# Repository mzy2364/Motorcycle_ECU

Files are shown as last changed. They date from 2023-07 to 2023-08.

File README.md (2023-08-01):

# Motorcycle_ECU

单缸摩托车发送机控制单元

视频地址 : <a href="https://www.bilibili.com/video/BV1r14y167MM/">https://www.bilibili.com/video/BV1r14y167MM/</a> 

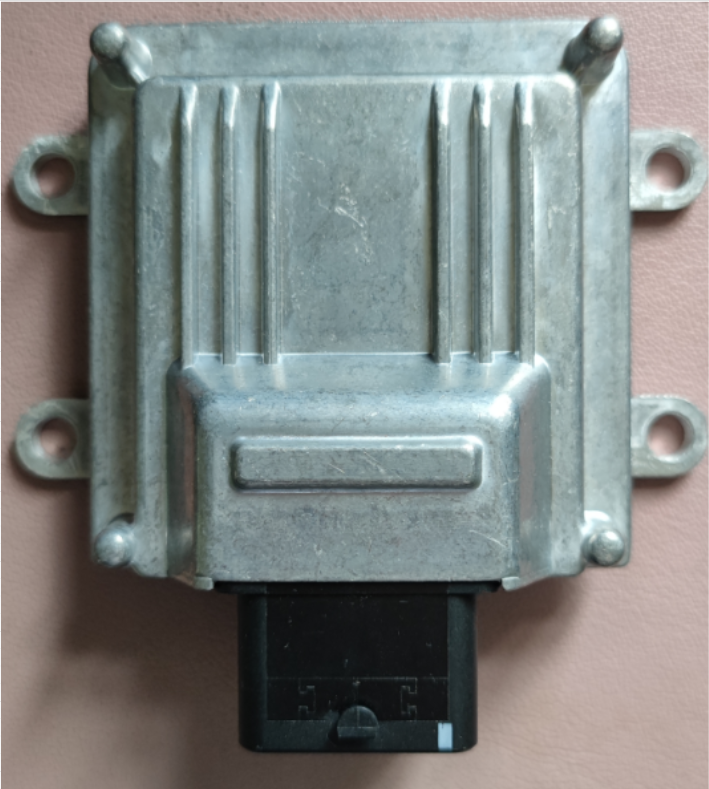
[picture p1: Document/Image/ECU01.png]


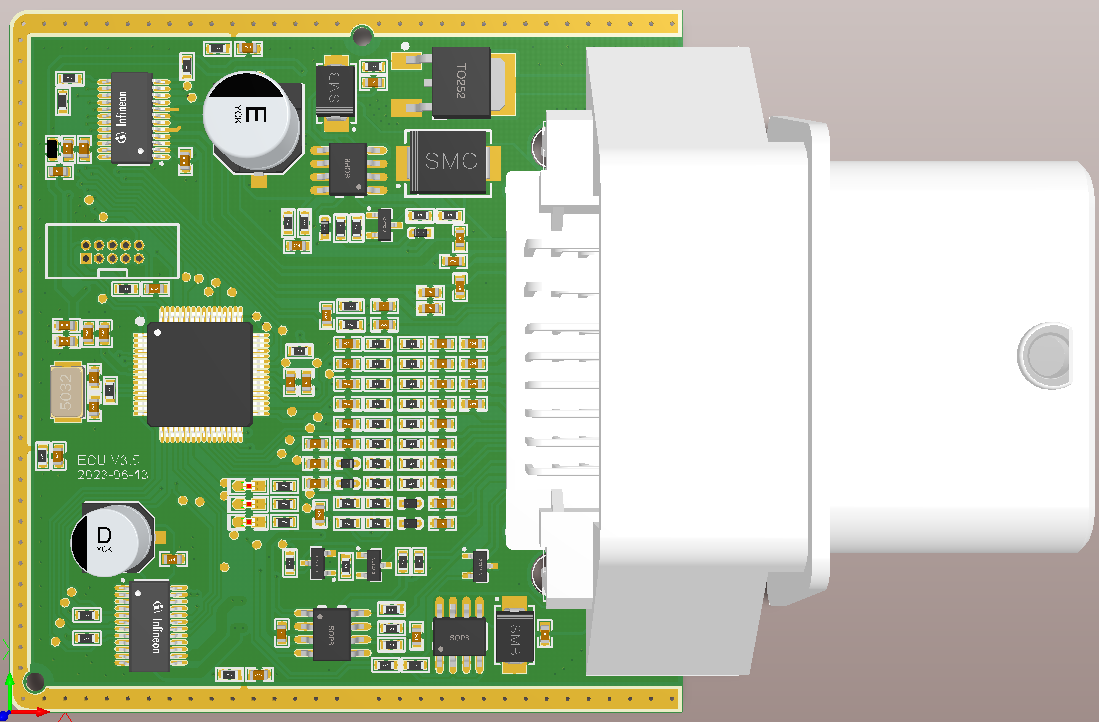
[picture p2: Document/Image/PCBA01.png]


### 支持功能

曲轴信号识别

点火线圈控制

喷油器控制

怠速电机控制

CAN 通讯

转速信号输出 / PWM输出

IgnON、Engine Stop 等开关识别

节气门位置传感器、进气歧管压力传感器、空气温度传感器、缸体温度传感器、氧传感器等

氧传感器加热

MIL 灯控制、继电器输出、燃油泵控制、怠速阀控制

### 硬件结构

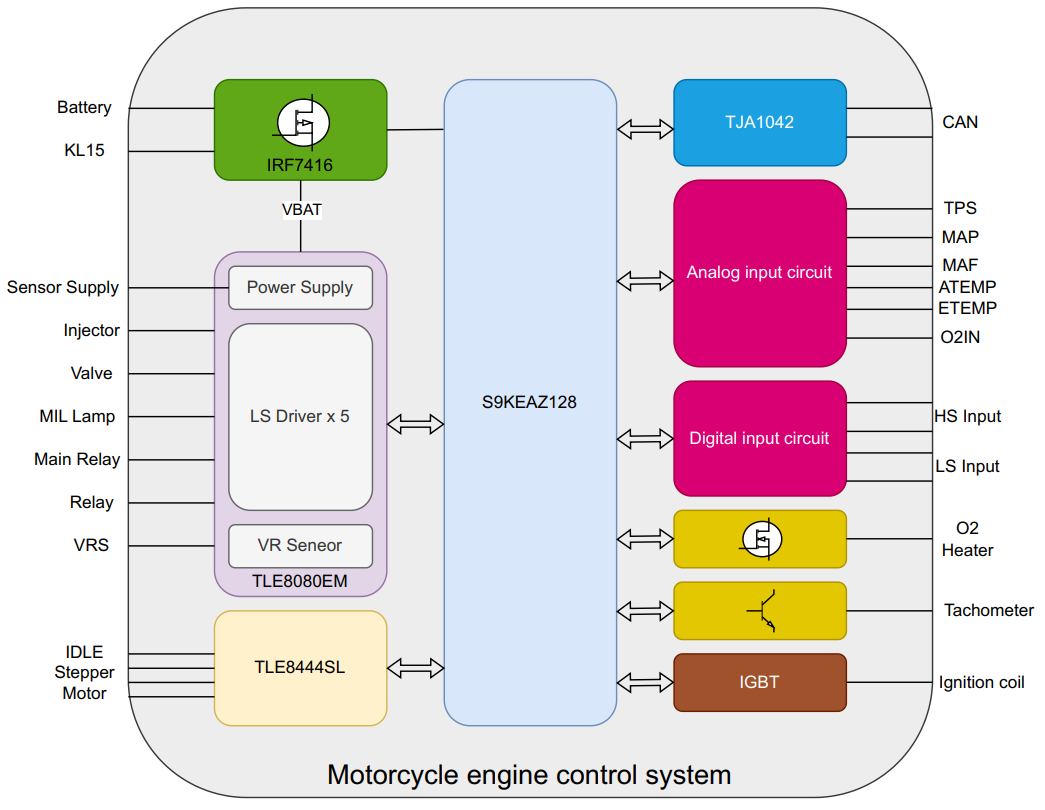
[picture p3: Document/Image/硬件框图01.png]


### 软件功能

仅提供支持发动机运转的基本功能，包括：

曲轴位置识别

喷油角度和脉宽计算

点火角度和蓄能时间计算

根据曲轴位置控制点火和喷油

根据进气歧管压力传感器识别冲程

CAN通讯，关键信息发送，基于 CAN 的简单标定

转速脉冲信号输出

燃油泵驱动

### 参考资料

https://www.nxp.com.cn/applications/automotive/electrification-and-powertrain/motorcycle-engine-control-unit-ecu-and-small-engine-control:MOTORCYCLE-ECU-SMALL-ENGINE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

https://www.st.com/zh/applications/powertrain-for-ice/single-cylinder-motorcycle-engine.html

https://www.infineon.com/cms/cn/applications/automotive/powertrain-systems/small-1-cylinder-combustion-engine-solution/

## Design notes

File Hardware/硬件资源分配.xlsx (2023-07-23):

LQFP64 | Pin Name | 默认值 | ALT0 | ALT1 | ALT2 | ALT3 | ALT4 | ALT5 | 所选资源 | 引脚网络名 | 功能区域
1 | PTD1 | 禁用 | PTD1 | KBI0_P25 | FTM2_CH3 | SPI1_MOSI |  |  | FTM2_CH3 | VRSOUT | 曲轴信号采集
2 | PTD0 | 禁用 | PTD0 | KBI0_P24 | FTM2_CH2 | SPI1_SCK |  |  | FTM2_CH2 |  | 曲轴缺齿中断用
3 | PTH7 | 禁用 | PTH7 | KBI1_P31 | PWT_IN1 |  |  |  | GPIO
4 | PTH6 | 禁用 | PTH6 | KBI1_P30 |  |  |  |  | GPIO
5 | PTE7 | 禁用 | PTE7 | KBI1_P7 | TCLK2 | FTM1_CH1 | CAN0_TX |  | GPIO/FTM1_CH1 | O_F_CH01/M | PWM以及转速信号输出
6 | PTH2 | 禁用 | PTH2 | KBI1_P26 | BUSOUT | FTM1_CH0 | CAN0_RX |  | FTM1_CH0 | O2HIN | 氧传感器加热
7 | VDD | VDD | VDD |  |  |  |  |  | VDD |  | 系统及电源
8 | VDDA | VDDA | VREFH | VDDA |  |  |  |  | VDD |  | 系统及电源
9 | VREFL | VREFL | VREFL |  |  |  |  |  | GND |  | 系统及电源
10 | VSS/ VSSA | VSS/ VSSA | VSSA | VSS |  |  |  |  | GND |  | 系统及电源
11 | PTB7 | EXTAL | PTB7 | KBI0_P15 | I2C0_SCL | EXTAL |  |  | OSC |  | 系统及电源
12 | PTB6 | XTAL | PTB6 | KBI0_P14 | I2C0_SDA | XTAL |  |  | OSC |  | 系统及电源
13 | PTI4 | 禁用 | PTI4 | IRQ
14 | PTH1 | 禁用 | PTH1 | KBI1_P25 | FTM2_CH1
15 | PTH0 | 禁用 | PTH0 | KBI1_P24 | FTM2_CH0
16 | PTE6 | 禁用 | PTE6 | KBI1_P6 |  |  |  |  | GPIO | MOTOR_EF2 | 电机驱动故障反馈
17 | PTE5 | 禁用 | PTE5 | KBI1_P5 |  |  |  |  | GPIO | MOTOR_IN2 | 电机驱动
18 | PTB5 | 禁用 | PTB5 | KBI0_P13 | FTM2_CH5 | SPI0_PCS | ACMP1_OUT |  | GPIO | MOTOR_EF1 | 电机驱动故障反馈
19 | PTB4 | NMI_b | PTB4 | KBI0_P12 | FTM2_CH4 | SPI0_MISO | ACMP1_IN2 | NMI_b | GPIO | MOTOR_IN4 | 电机驱动
20 | PTC3 | ADC0_SE11 | PTC3 | KBI0_P19 | FTM2_CH3 | ADC0_SE11 |  |  | GPIO | MOTOR_INH | 电机驱动使能
21 | PTC2 | ADC0_SE10 | PTC2 | KBI0_P18 | FTM2_CH2 | ADC0_SE10 |  |  | GPIO | LED_B | LED_B
22 | PTD7 | 禁用 | PTD7 | KBI0_P31 | UART2_TX |  |  |  | GPIO | LED_G | LEB_G
23 | PTD6 | 禁用 | PTD6 | KBI0_P30 | UART2_RX |  |  |  | GPIO | LED_R | LEB_R
24 | PTD5 | 禁用 | PTD5 | KBI0_P29 | PWT_IN0 |  |  |  | GPIO/PWT_IN0 | I_S_CH04/M | 高低边输入CH4
25 | PTC1 | ADC0_SE9 | PTC1 | KBI0_P17 | FTM2_CH1 | ADC0_SE9
26 | PTC0 | ADC0_SE8 | PTC0 | KBI0_P16 | FTM2_CH0 | ADC0_SE8 |  |  | GPIO | I_S_CH03/M | 高低边输入CH3
27 | PTF7 | ADC0_SE15 | PTF7 | KBI1_P15 | ADC0_SE15 |  |  |  | GPIO | I_S_CH01/M | 高低边输入CH1
28 | PTF6 | ADC0_SE14 | PTF6 | KBI1_P14 | ADC0_SE14 |  |  |  | GPIO | I_S_CH02/M | 高低边输入CH2
29 | PTF5 | ADC0_SE13 | PTF5 | KBI1_P13 | ADC0_SE13 |  |  |  | ADC0_SE13 | ETEMP_M | 模拟量输入ETEMP
30 | PTF4 | ADC0_SE12 | PTF4 | KBI1_P12 | ADC0_SE12 |  |  |  | ADC0_SE12 | TPS_M | 模拟量输入TPS
31 | PTB3 | ADC0_SE7 | PTB3 | KBI0_P11 | SPI0_MOSI | FTM0_CH1 | ADC0_SE7 |  | FTM0_CH1 | MOTOR_IN3 | 电机驱动
32 | PTB2 | ADC0_SE6 | PTB2 | KBI0_P10 | SPI0_SCK | FTM0_CH0 | ADC0_SE6 |  | FTM0_CH0 | MOTOR_IN1 | 电机驱动
33 | PTB1 | ADC0_SE5 | PTB1 | KBI0_P9 | UART0_TX | ADC0_SE5 |  |  | ADC0_SE5 | ATEMP_M | 模拟量输入ATEMP
34 | PTB0 | ADC0_SE4 | PTB0 | KBI0_P8 | UART0_RX | PWT_IN1 | ADC0_SE4 |  | ADC0_SE4 | MAF_M | 模拟量输入MAF
35 | PTF3 | 禁用 | PTF3 | KBI1_P11 | UART1_TX
36 | PTF2 | 禁用 | PTF2 | KBI1_P10 | UART1_RX
37 | PTA7 | ADC0_SE3 | PTA7 | KBI0_P7 | FTM2_FLT2 | ACMP1_IN1 | ADC0_SE3 |  | ADC0_SE3 | O2IN_M | 模拟量输入O2IN
38 | PTA6 | ADC0_SE2 | PTA6 | KBI0_P6 | FTM2_FLT1 | ACMP1_IN0 | ADC0_SE2 |  | ADC0_SE2 | MAP_M | 模拟量输入MAP
39 | PTE4 | 禁用 | PTE4 | KBI1_P4
40 | VSS | VSS | VSS |  |  |  |  |  | GND |  | 系统及电源
41 | VDD | VDD | VDD |  |  |  |  |  | VDD |  | 系统及电源
42 | PTF1 | 禁用 | PTF1 | KBI1_P9 | FTM2_CH1 |  |  |  | FTM2_CH1 | COIL_DRV | 点火线圈驱动
43 | PTF0 | 禁用 | PTF0 | KBI1_P8 | FTM2_CH0 |  |  |  | FTM2_CH0 | INJ_CTRL | 喷油嘴驱动
44 | PTD4 | 禁用 | PTD4 | KBI0_P28
45 | PTD3 | 禁用 | PTD3 | KBI0_P27 | SPI1_PCS
46 | PTD2 | 禁用 | PTD2 | KBI0_P26 | SPI1_MISO |  |  |  |  | VCC_CTRL | 电源使能
47 | PTA3 | 禁用 | PTA3 | KBI0_P3 | UART0_TX | I2C0_SCL
48 | PTA2 | 禁用 | PTA2 | KBI0_P2 | UART0_RX | I2C0_SDA |  |  | GPIO
49 | PTA1 | ADC0_SE1 | PTA1 | KBI0_P1 | FTM0_CH1 | I2C0_ 4WSDAOUT | ACMP0_IN1 | ADC0_SE1 | ADC0_SE1 | VBAT_ADC | 电源电压采集
50 | PTA0 | ADC0_SE0 | PTA0 | KBI0_P0 | FTM0_CH0 | I2C0_ 4WSCLOUT | ACMP0_IN0 | ADC0_SE0 | GPIO | VALVE_CTRL | 怠速阀控制
51 | PTC7 | 禁用 | PTC7 | KBI0_P23 | UART1_TX | CAN0_TX |  |  | CAN0_TX | CAN_TX | CAN
52 | PTC6 | 禁用 | PTC6 | KBI0_P22 | UART1_RX | CAN0_RX |  |  | CAN0_RX | CAN_RX | CAN
53 | PTE3 | 禁用 | PTE3 | KBI1_P3 | SPI0_PCS |  |  |  | SPI0_PCS | SPI_CS | TLE8080-SPI驱动
54 | PTE2 | 禁用 | PTE2 | KBI1_P2 | SPI0_MISO | PWT_IN0 |  |  | SPI0_MISO | SPI_MISO | TLE8080-SPI驱动
55 | PTG3 | 禁用 | PTG3 | KBI1_P19
56 | PTG2 | 禁用 | PTG2 | KBI1_P18
57 | PTG1 | 禁用 | PTG1 | KBI1_P17
58 | PTG0 | 禁用 | PTG0 | KBI1_P16
59 | PTE1 | 禁用 | PTE1 | KBI1_P1 | SPI0_MOSI | I2C1_SCL |  |  | SPI0_MOSI | SPI_MOSI | TLE8080-SPI驱动
60 | PTE0 | 禁用 | PTE0 | KBI1_P0 | SPI0_SCK | TCLK1 | I2C1_SDA |  | SPI0_SCK | SPI_SCK | TLE8080-SPI驱动
61 | PTC5 | 禁用 | PTC5 | KBI0_P21 | FTM1_CH1 | RTC_CLKOUT
62 | PTC4 | SWD_CLK | PTC4 | KBI0_P20 | RTC_CLKOUT | FTM1_CH0 | ACMP0_IN2 | SWD_CLK | SWCLK |  | 系统及电源
63 | PTA5 | RESET_b | PTA5 | KBI0_P5 | IRQ | TCLK0 | RESET_b |  | RESET |  | 系统及电源
64 | PTA4 | SWD_DIO | PTA4 | KBI0_P4 | ACMP0_OUT | SWD_DIO |  |  | SWDIO |  | 系统及电源

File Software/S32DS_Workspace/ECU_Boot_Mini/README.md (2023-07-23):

# ECU_Boot_Mini

ECU 最小 Boot，仅提供跳转功能，不支持 APP 更新

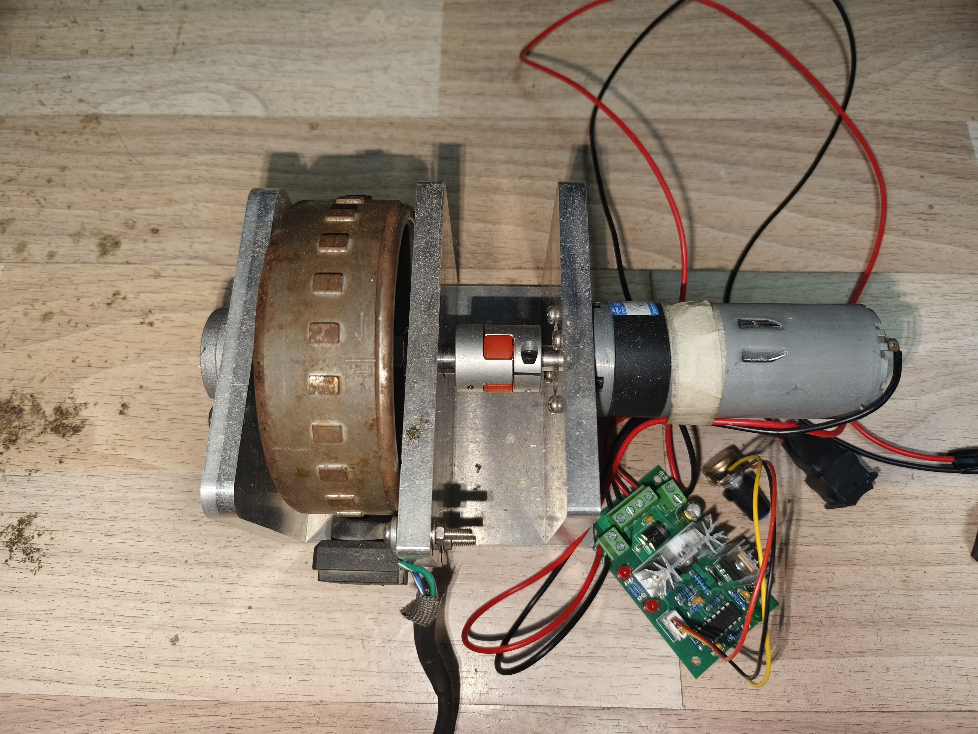
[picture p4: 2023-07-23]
Hardware/曲轴模拟器.jpg

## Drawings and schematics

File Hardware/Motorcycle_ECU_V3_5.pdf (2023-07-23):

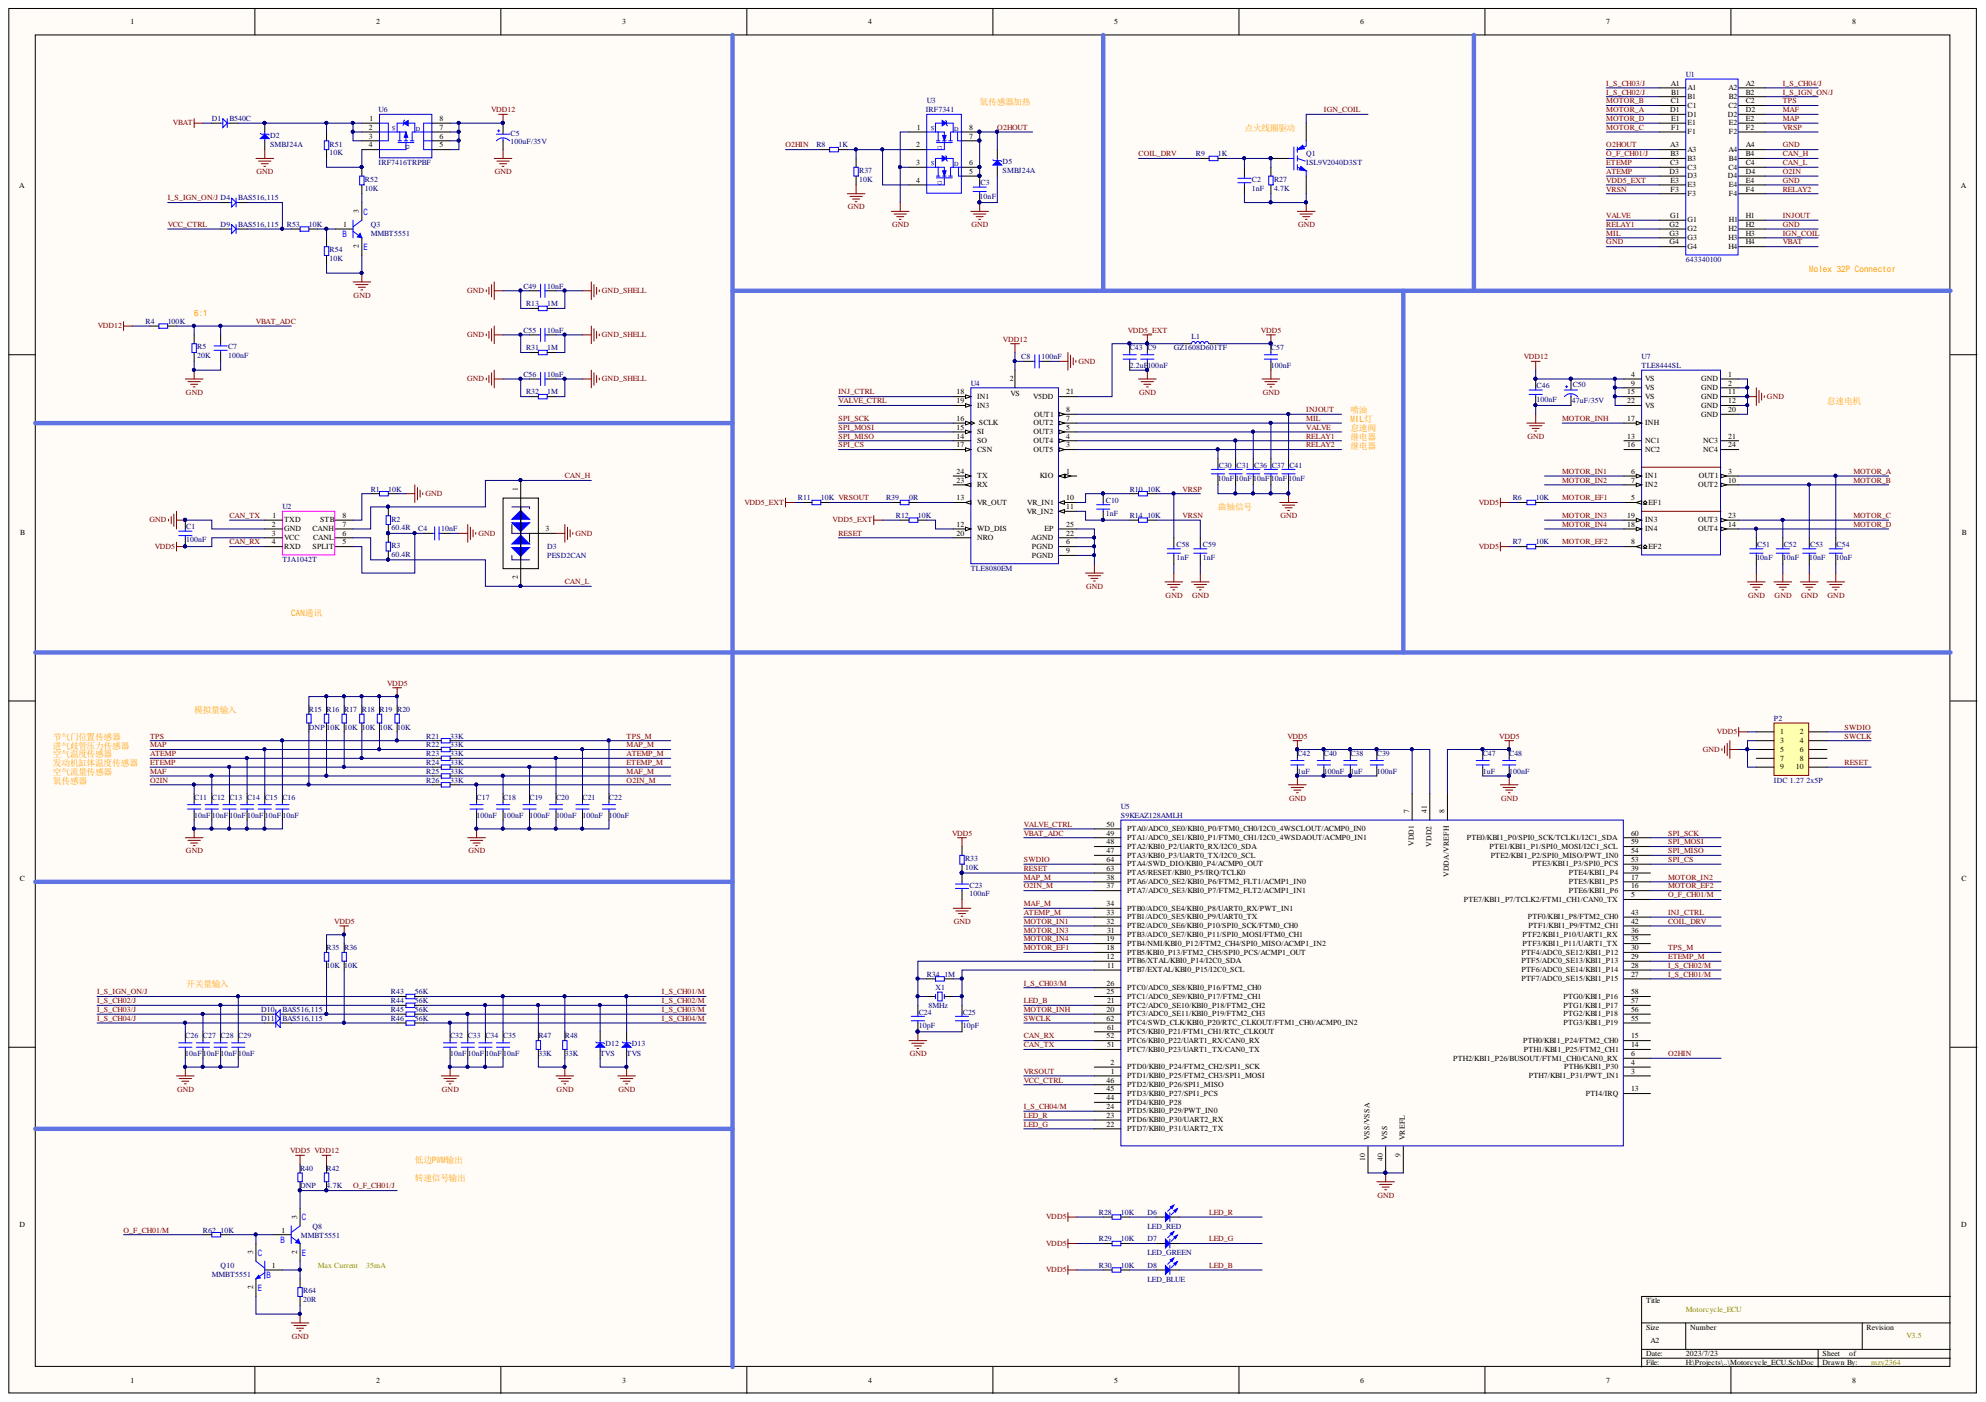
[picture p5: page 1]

IL灯 怠速阀 继电器 继电器

节气门位置传感器
进气歧管压力传感器 空气温度传感器 发动机缸体温度传感器 空气流量传感器

PTB7/EXTAL/KBI0_P15/I2C0_SCL 11

I_S_CH03/M LED_B | PTC0/ADC0_SE8/KBI0_P16/FTM2_CH0 26 PTC1/ADC0_SE9/KBI0_P17/FTM2_CH1 25

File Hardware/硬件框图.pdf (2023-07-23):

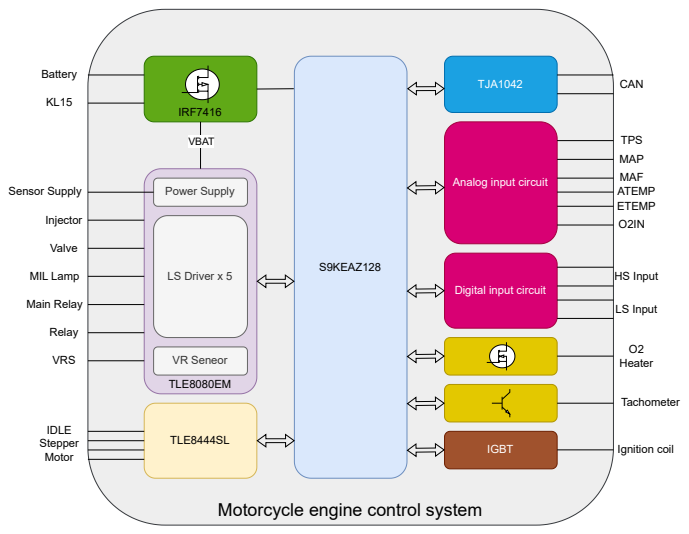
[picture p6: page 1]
S9KEAZ128; VR Seneor; Power Supply; LS Driver x 5; TLE8080EM; TJA1042; TLE8444SL; IRF7416; IGBT; Battery; VBAT; Sensor Supply; Injector; Main Relay; Valve; Relay; MIL Lamp; VRS; IDLE Stepper Motor; CAN; TPS; MAP; MAF ATEMP ETEMP; HS Input; LS Input; O2 Heater; Tachometer; Ignition coil

Analog input circuit

Digital input circuit

Motorcycle engine control system

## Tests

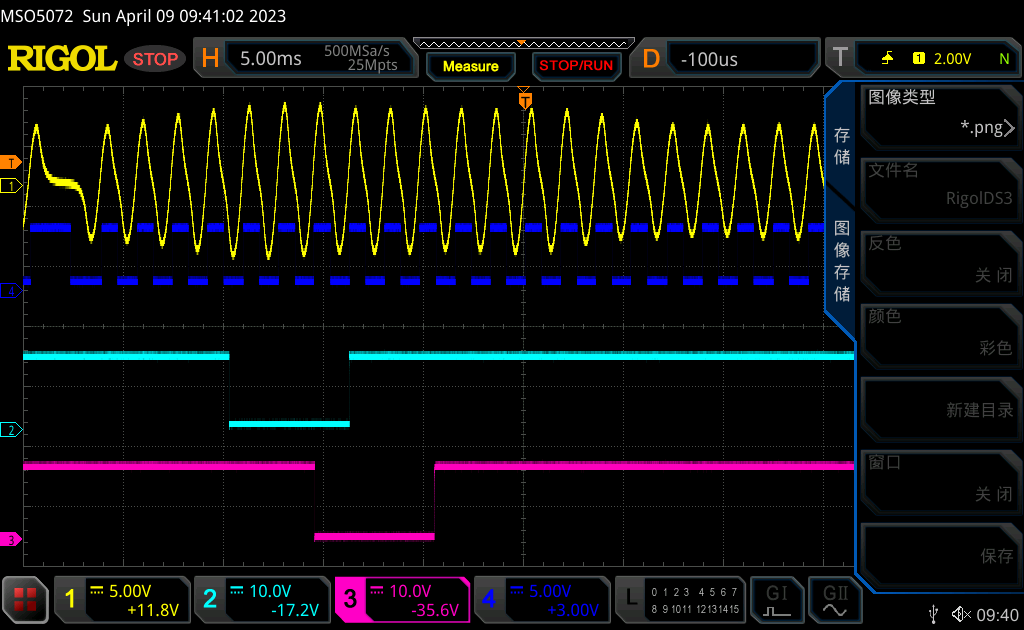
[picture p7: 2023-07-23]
Testfile/ECU时序信号CH2点火CH3喷油.png

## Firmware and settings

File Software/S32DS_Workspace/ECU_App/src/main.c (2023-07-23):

/*
 * main implementation: use this 'C' sample to create your own application
 *
 */


#include "derivative.h" /* include peripheral declarations SSKEAZ128M4 */
#include "task.h"

int main(void)
{
	task_init();

	for(;;)
	{
		task_scheduler();
	}

    /* to avoid the warning message for GHS: statement is unreachable*/
#if defined (__ghs__)
#pragma ghs nowarning 111
#endif
#if defined (__ICCARM__)
#pragma diag_suppress=Pe111
#endif
	return 0;
}

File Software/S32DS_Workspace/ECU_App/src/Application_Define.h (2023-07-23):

/*
 * Application_Define.h
 *
 *  Created on: 2023年3月4日
 *      Author: mzy2364
 */

#ifndef APPLICATION_DEFINE_H_
#define APPLICATION_DEFINE_H_

#ifdef __cplusplus
extern "C"{
#endif

#include "derivative.h"

//定义曲轴上面的齿数
#define NUMBER_OF_TEETH 	24
//四冲程一个循环的齿数
#define NUMBER_OF_TEETH_4C NUMBER_OF_TEETH * 2
//每个齿对应的度数
#define DEGREES_PER_TOOTH (360 / NUMBER_OF_TEETH)


  //Indicate what tooth represents TDC based on detection method above.
  //Use zero as reference for missing tooth.  Tooth one define as first detected
  //edge after the missing tooth gap.  Tooth count goes from 0 to NUMBER_OF_TEETH-1
  #define TDC_TOOTH 9
    //This results in an angle relative to TDC to be used in the application.
    #define TDC_ANGLE (TDC_TOOTH * DEGREES_PER_TOOTH)
    
  //Specify the orientation between cylinders 1 and 2 if it is a two cylinder engine.
  #ifdef TWO_CYLINDER
  //Standard orientation is 180 degrees for two stroke.
  //Standard orientation is 360 degrees for four stroke.
  #define CYLINDER_OFFSET_ANGLE 180
  #endif

  //Define how many spark events per cycle are performed.
  //Currently only 1 event supported
  #define SPARK_EVENTS_NUM 1

  //Define the angle when fuel injection starts in degrees.  This is relative to the 
  //missing tooth.  Application uses fixed start time for fuel injection 
  //and makes the pulse time from this angle.  
  //Typical application will use TDC.    
  #define FUEL1_REF_ANGLE  TDC_ANGLE
    //This results in an angle for when the fuel is injector for the 
    //second cylinder if it is defined.
    #ifdef TWO_CYLINDER
      //For a two stroke engine, this is just the offset.
      #ifdef TWO_STROKES
        #define FUEL2_REF_ANGLE  (TDC_ANGLE + CYLINDER_OFFSET_ANGLE)
      #endif
      //For a four stroke engine, we have to compensate as we need 
      //a reference angle to start the engine in two stroke mode.  
      //A separate reference angle is created later for when the application
      //is synchronized to the four stroke process.  
      #ifdef FOUR_STROKES
        #define FUEL2_REF_ANGLE  (FUEL1_REF_ANGLE + CYLINDER_OFFSET_ANGLE - 180)
        //This definition only works for the 360 degree offset case.  
      #endif      
    #endif
    
    
    //This also results in a secondary reference angle if four stroke 
    //application is defined.
    #ifdef FOUR_STROKES
      //Create the reference angle for four stroke operation.
      #define FUEL1_REF_ANGLE_4C  FUEL1_REF_ANGLE
      #ifdef TWO_CYLINDER
        //Create the reference angle for four stroke operation.
        #define FUEL2_REF_ANGLE_4C  FUEL1_REF_ANGLE + CYLINDER_OFFSET_ANGLE
      #endif
    #endif


//Set the engine running parameters
//Engine running parameters
//Minimum engine speed that defines the engine as running.
//This is tooth period counts based on 1.6us timer tic.
#define Stall_Speed 300 // 500 RPM

//Maximum engine speed that defines overrunning.
//This is tooth period counts based on 1.6us timer tic.
#define Over_Speed 8000   // 8000 RPM

//Engine speed required to recover from an over speed condition
//This is tooth period counts based on 1.6us timer tic.
#define Over_Speed_Recovery 416 //7500 RPM
   
   
/*Crankshaft Synchronization Parameters*****************************************/

  //Set the minimum RPM for engine rotation
  #define RPM_MIN 200
    //This results in a maximum tooth period that is valid.
    //Application uses this value in terms of timer tics.
                                
  //Set the maximum RPM for engine rotation
  #define RPM_MAX 9000
    //This results in a minimum tooth period that is valid.
    //Application uses this value in terms of timer tics.
      
  //Specify how much the tooth period can vary from tooth to tooth.
  //This is the tooth tolerance and is based on manufacturing of the 
  //teeth on the flywheel and the pulsation of the engine.  
  #define POS_PERIOD_PERCENTAGE 50
  #define NEG_PERIOD_PERCENTAGE 50
    
  //Specify the length of time before synchronization is lost when a 
  //tooth is not detected, based on the last tooth period.
  #define CRANKSHAFT_TIMEOUT_PERCENTAGE 80  
  //A default timeout is set for conditions prior to getting the first 
  //tooth period time.  This is set for the minimum RPM defined.    

  //Specify what gap ratio is for a missing tooth compared to a normal tooth.
  //This is typically 2 for a single missing tooth.
  //This results in minimum and maximum values of the gap ratio based on
  //tooth tolerance specified above.
  #define GAP_RATIO 2
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

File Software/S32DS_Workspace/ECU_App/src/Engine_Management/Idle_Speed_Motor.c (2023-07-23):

/*
 * Idle_Speed_Motor.c
 *
 *  Created on: 2023年3月21日
 *      Author: mzy2364
 */



/*******************************************************************************
* include files                                                 
*******************************************************************************/
#include "Idle_Speed_Motor.h"
#include "ftm.h"
#include "gpio.h"
/*******************************************************************************
* Defines                                                                
*******************************************************************************/

/*******************************************************************************
* Macros                                                                
*******************************************************************************/

/*******************************************************************************
* Global Constant definition                         
*******************************************************************************/

/*******************************************************************************
* Local Constant definition                         
*******************************************************************************/

/*******************************************************************************
* Global Variables definition                         
*******************************************************************************/

/*******************************************************************************
* Local Variables definition                         
*******************************************************************************/
static uint8_t motor_state = 0;
motor_state_t ism_state = MOTOR_STOPPED;
uint32_t motor_angle = 0;
uint32_t idle_motor_position = 0;
/*******************************************************************************
* Local Functions prototypes                         
*******************************************************************************/
static void ftm0_isr(void);

/*******************************************************************************
*  Global Functions Body                                   
*******************************************************************************/

/**
  * @brief 
  * @param void
  * @retval	void
  * @note
  */
void idle_speed_motor_init(void)
{
//	FTM_ConfigType FTM0_Config = {0};
//	FTM_ChParamsType FTM0CH1_Config = {0};
//	FTM_ChParamsType FTM0CH0_Config = {0};
//
//	SIM->PINSEL |= SIM_PINSEL_FTM0PS1_MASK;	//FTM0_CH1 通道映射到 PTB3 上
//	SIM->PINSEL |= SIM_PINSEL_FTM0PS0_MASK;	//FTM0_CH0 通道映射到 PTB2 上
//
//	FTM0_Config.modulo = 9999;
//	FTM0_Config.combine = FTM_COMBINE_COMBINE0_MASK|FTM_COMBINE_SYNCEN0_MASK;
//	FTM0_Config.clk_source = FTM_CLOCK_SYSTEMCLOCK;
//	FTM0_Config.prescaler = FTM_CLOCK_PS_DIV1;
//	//FTM0_Config.mode = 1;
//	FTM0_Config.toie = 1;
//
//
//	FTM0CH0_Config.ctrl.bits.bMode = FTM_PWMMODE_COMBINE;
//	FTM0CH0_Config.ctrl.bits.bPWMPol = FTM_PWM_HIGHTRUEPULSE;
//	FTM0CH0_Config.u16CnV = 5000;
//
//
//	FTM0CH1_Config.ctrl.bits.bMode = FTM_PWMMODE_COMBINE;
//	FTM0CH1_Config.ctrl.bits.bPWMPol = FTM_PWM_HIGHTRUEPULSE;
//	FTM0CH1_Config.u16CnV = 5000;
//
//	FTM_SetCallback(FTM0, ftm0_isr);
//	FTM_ChannelInit(FTM0,0,FTM0CH0_Config);
//	FTM_ChannelInit(FTM0,1,FTM0CH1_Config);
//	FTM_Init(FTM0,&FTM0_Config);   /* Generate PWM signal */

	SIM_SOPT0 &= ~SIM_SOPT0_NMIE_MASK;
	CONFIG_PIN_AS_GPIO(MOTOR_IN1_PORT,MOTOR_IN1_PIN,OUTPUT);
	CONFIG_PIN_AS_GPIO(MOTOR_IN2_PORT,MOTOR_IN2_PIN,OUTPUT);
	CONFIG_PIN_AS_GPIO(MOTOR_IN3_PORT,MOTOR_IN3_PIN,OUTPUT);
	CONFIG_PIN_AS_GPIO(MOTOR_IN4_PORT,MOTOR_IN4_PIN,OUTPUT);

//	CONFIG_PIN_AS_GPIO(MOTOR_EF1_PORT,MOTOR_EF1_PIN,INPUT);
//	CONFIG_PIN_AS_GPIO(MOTOR_EF2_PORT,MOTOR_EF2_PIN,INPUT);

	CONFIG_PIN_AS_GPIO(MOTOR_INH_PORT,MOTOR_INH_PIN,OUTPUT);
	OUTPUT_SET(MOTOR_INH_PORT,MOTOR_INH_PIN);
}

void A_negative_current(void)
{
	OUTPUT_CLEAR(MOTOR_IN2_PORT,MOTOR_IN2_PIN);
	OUTPUT_CLEAR(MOTOR_IN1_PORT,MOTOR_IN1_PIN);
}

void A_positive_current(void)
{
	OUTPUT_SET(MOTOR_IN2_PORT,MOTOR_IN2_PIN);
	OUTPUT_SET(MOTOR_IN1_PORT,MOTOR_IN1_PIN);
}

void A_no_current(void)
{
	OUTPUT_SET(MOTOR_IN2_PORT,MOTOR_IN2_PIN);
	OUTPUT_CLEAR(MOTOR_IN1_PORT,MOTOR_IN1_PIN);
}

void B_negative_current(void)
{
	OUTPUT_CLEAR(MOTOR_IN4_PORT,MOTOR_IN4_PIN);
	OUTPUT_CLEAR(MOTOR_IN3_PORT,MOTOR_IN3_PIN);
}

void B_positive_current(void)
{
	OUTPUT_SET(MOTOR_IN4_PORT,MOTOR_IN4_PIN);
	OUTPUT_SET(MOTOR_IN3_PORT,MOTOR_IN3_PIN);
}

void B_no_current(void)
{
	OUTPUT_SET(MOTOR_IN4_PORT,MOTOR_IN4_PIN);
	OUTPUT_CLEAR(MOTOR_IN3_PORT,MOTOR_IN3_PIN);
}

/**
  * @brief 步进电机向前运动
  * @param void
  * @retval	void
  * @note
  */
void idle_speed_motor_forward(void)
{
	switch(motor_state)
	{
	case 0:
		B_positive_current();
		A_no_current();
		motor_state++;
		break;
	case 1:
		B_positive_current();
		A_positive_current();
		motor_state++;
		break;
	case 2:
		B_no_current();
		A_positive_current();
		motor_state++;
		break;
	case 3:
		B_negative_current();
		A_positive_current();
		motor_state++;
		break;
	case 4:
		B_negative_current();
		A_no_current();
		motor_state++;
		break;
	case 5:
		B_negative_current();
		A_negative_current();
		motor_state++;
		break;
	case 6:
		B_no_current();
		A_negative_current();
		motor_state++;
		break;
	case 7:
		B_positive_current();
		A_negative_current();
		motor_state = 0;
		idle_motor_position++;
		break;
	default:
		break;
	}
}

/**
  * @brief 步进电机向后运动
  * @param void
  * @retval	void
  * @note
  */
void idle_speed_motor_backward(void)
{
	switch(motor_state)
	{
	case 0:
		A_positive_current();
		B_no_current();
		motor_state++;
		break;
	case 1:
		A_positive_current();
		B_positive_current();
		motor_state++;
		break;
	case 2:
		A_no_current();
		B_positive_current();
		motor_state++;
		break;
	case 3:
		A_negative_current();
		B_positive_current();
		motor_state++;
		break;
	case 4:
		A_negative_current();
		B_no_current();
		motor_state++;
		break;
	case 5:
		A_negative_current();
		B_negative_current();
		motor_state++;
		break;
	case 6:
		A_no_current();
		B_negative_current();
		motor_state++;
		break;
	case 7:
		A_positive_current();
		B_negative_current();
		motor_state = 0;
		idle_motor_position--;
		break;
	default:
		break;
	}
}



void motor_task(void)
{
	//if(idle_motor_position < 10)
	{
		idle_speed_motor_forward();
	}
//	if(ism_state != MOTOR_STOPPED)
//	{
//		if(ism_state == MOTOR_OPENING)
//		{
//			idle_speed_motor_forward();
//			if(idle_motor_position == 0)
//			{
//				ism_state = MOTOR_STOPPED;
//			}
//		}
//		else if(ism_state == MOTOR_CLOSING)
//		{
//			idle_speed_motor_backward();
//			if(idle_motor_position >= 10)
//			{
//				ism_state = MOTOR_STOPPED;
//			}
//		}
//	}
}

/**
  * @brief FTM0中断回调函数
  * @param void
  * @retval	void
  * @note
  */
static void ftm0_isr(void)
{
	if(FTM_GetOverFlowFlag(FTM0) && (FTM0->SC & FTM_SC_TOIE_MASK))
	{
		FTM_ClrOverFlowFlag(FTM0);
	}
}

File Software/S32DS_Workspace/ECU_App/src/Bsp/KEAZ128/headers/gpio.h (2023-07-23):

/******************************************************************************
*
* Freescale Semiconductor Inc.
* (c) Copyright 2013 Freescale Semiconductor, Inc.
* ALL RIGHTS RESERVED.
*
***************************************************************************
*
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
***************************************************************************//*!
*
* @file GPIO.h
*
* @author Freescale
*
* @brief provide common GPIO utilities. 
*
*******************************************************************************/

#ifndef GPIO_H_
#define GPIO_H_

/*******************************************************************************
* Includes
*******************************************************************************/
#include "derivative.h"


/*******************************************************************************
* Constants
********************************************************************************/


/*******************************************************************************
* Macros
********************************************************************************/

/***********************************************************
 * 
 * Ports mapped to GPIOA,GPIOB and GPIOC registers
 * 
 **********************************************************/
#if defined(MCU_SKEAZ1284)
#define PTA     GPIOA_BASE_PTR
#elif defined(MCU_SKEAZN642)
#define PTA		GPIOA //PTA defined in defice header as GPIOA. Not a problem since GPIOA=GPIOA_BASE_PTR
#else
/* Define PTA for your device. */
#endif

#define PTB     GPIOA_BASE_PTR
#define PTC     GPIOA_BASE_PTR
#define PTD     GPIOA_BASE_PTR

#define PTE     GPIOB_BASE_PTR
#define PTF		GPIOB_BASE_PTR
#define PTG		GPIOB_BASE_PTR
#define PTH		GPIOB_BASE_PTR

#if defined(MCU_SKEAZ1284)
#define PTI		GPIOC_BASE_PTR
#elif defined(MCU_SKEAZN642)
/* KEAZN64 has no PTI. */
#else
/* If your device has more ports, define them here. */
#endif

/***********************************************************
 * 
 * Input/Output macro
 * 
 **********************************************************/
#define OUTPUT  1
#define INPUT	0

/***********************************************************
 * 
 * GPIO configuration macro
 * 
 **********************************************************/
#define CONFIG_PIN_AS_GPIO(port,port_pin,mode)    	XCONFIG_PIN_AS_GPIO(port,port_pin,mode)
#define XCONFIG_PIN_AS_GPIO(port,port_pin,mode)   	(mode == 0) ? (port->PDDR &=~(1<< port_pin)) : (port->PDDR |= (1 << port_pin)) 

/***********************************************************
 * 
 * Enable and Disable input macro
 * 
 **********************************************************/
#define ENABLE_INPUT(port,port_pin) 				XENABLE_INPUT(port,port_pin)
#define XENABLE_INPUT(port,port_pin)				port->PIDR &=~ (1<<port_pin)

#define DISABLE_INPUT(port,port_pin) 				XDISABLE_INPUT(port,port_pin)
#define XDISABLE_INPUT(port,port_pin)				port->PIDR |= (1<<port_pin)

/***********************************************************
 * 
 * Enable and Disable pullup resistor macro
 * 
 **********************************************************/
#define ENABLE_PULLUP(port,port_pin) 				XENABLE_PULLUP(port,port_pin) 	
#if defined(MCU_SKEAZ1284)
#define XENABLE_PULLUP(port,port_pin) 				if(port==GPIOA_BASE_PTR){PORT_BASE_PTR->PUE0 |= (1<<port_pin);} else if(port==GPIOB_BASE_PTR){PORT_BASE_PTR->PUE1|=(1<<port_pin);} else {PORT_BASE_PTR->PUE2|=(1<<port_pin);}
#elif defined(MCU_SKEAZN642)
#define XENABLE_PULLUP(port,port_pin) 				if(port==GPIOA_BASE_PTR){PORT_BASE_PTR->PUE0 |= (1<<port_pin);} else {PORT_BASE_PTR->PUE1|=(1<<port_pin);}
#else
/* Implement this function for your device. */
#endif

#define DISABLE_PULLUP(port,port_pin) 				XDISABLE_PULLUP(port,port_pin) 	
#if defined(MCU_SKEAZ1284)
#define XDISABLE_PULLUP(port,port_pin) 				if(port==GPIOA_BASE_PTR){PORT_BASE_PTR->PUE0 &=~ (1<<port_pin);} else if(port==GPIOB_BASE_PTR){PORT_BASE_PTR->PUE1 &=~ (1<<port_pin);} else {PORT_BASE_PTR->PUE2 &=~(1<<port_pin);}
#elif defined(MCU_SKEAZN642)
#define XDISABLE_PULLUP(port,port_pin) 				if(port==GPIOA_BASE_PTR){PORT_BASE_PTR->PUE0 &=~ (1<<port_pin);} else {PORT_BASE_PTR->PUE1 &=~ (1<<port_pin);}
#else
/* Implement this function for your device. */
#endif

/***********************************************************
 * 
 * Output set macro
 * 
 **********************************************************/
#define OUTPUT_SET(port,port_pin)					XOUTPUT_SET(port,port_pin)
#define XOUTPUT_SET(port,port_pin)					port->PSOR |=(1<<port_pin)

/***********************************************************
 * 
 * Output clear macro
 * 
 **********************************************************/
#define OUTPUT_CLEAR(port,port_pin)					XOUTPUT_CLEAR(port,port_pin)		
#define XOUTPUT_CLEAR(port,port_pin)				port->PCOR |=(1<<port_pin)
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

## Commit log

2023-07-23 增加喷油脉宽
2023-07-31 修复远端无法显示图片的BUG
2023-08-01 增加视频地址
